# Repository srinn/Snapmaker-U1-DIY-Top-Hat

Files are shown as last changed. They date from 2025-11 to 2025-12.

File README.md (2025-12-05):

# Snapmaker U1 DIY Top Hat By. Srin
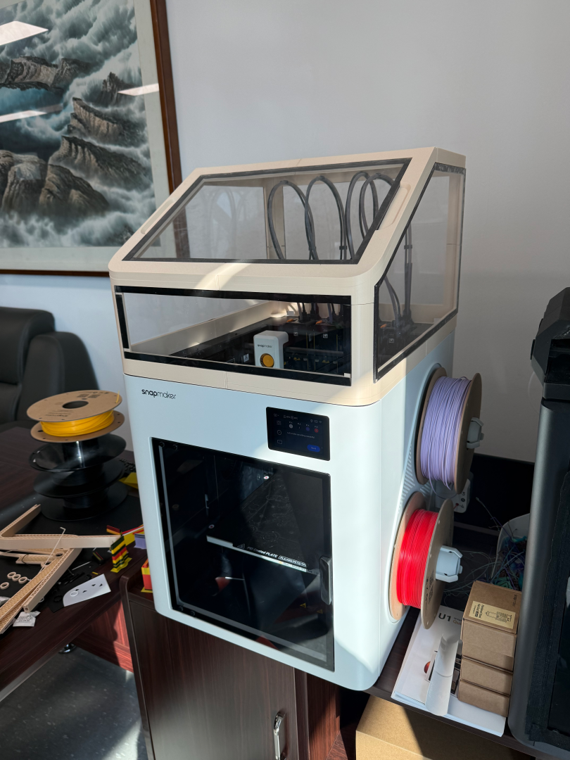
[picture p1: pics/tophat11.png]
tophat

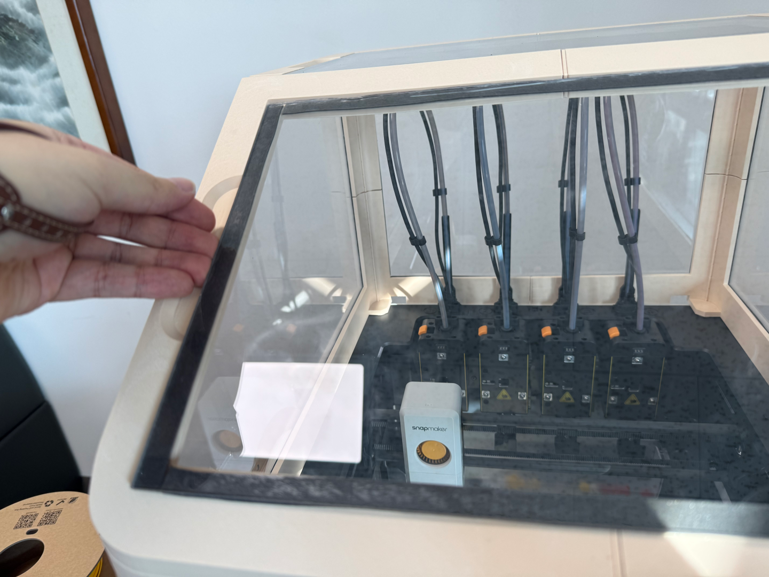
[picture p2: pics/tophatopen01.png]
tophat open

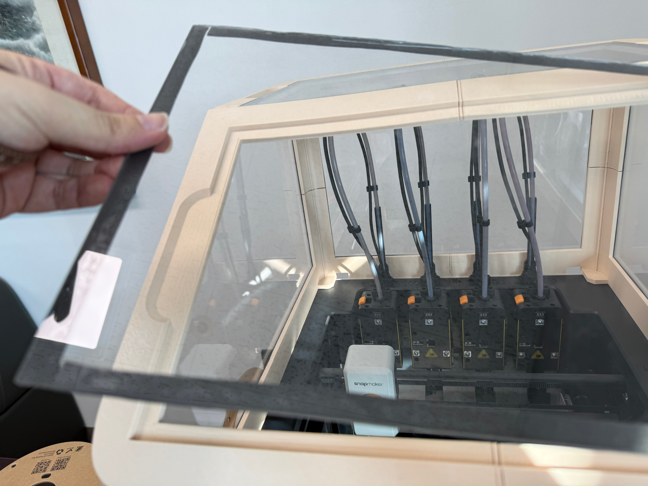
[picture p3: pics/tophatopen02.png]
tophat open

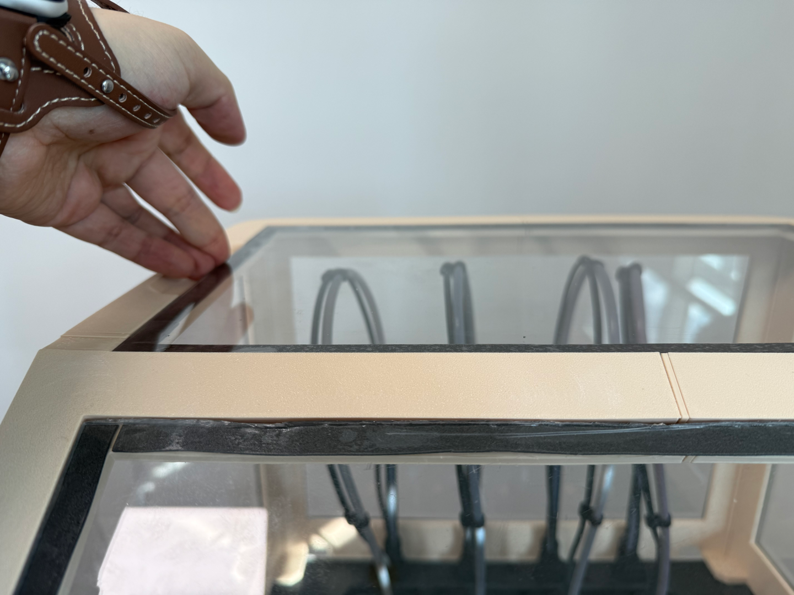
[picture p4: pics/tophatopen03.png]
tophat open

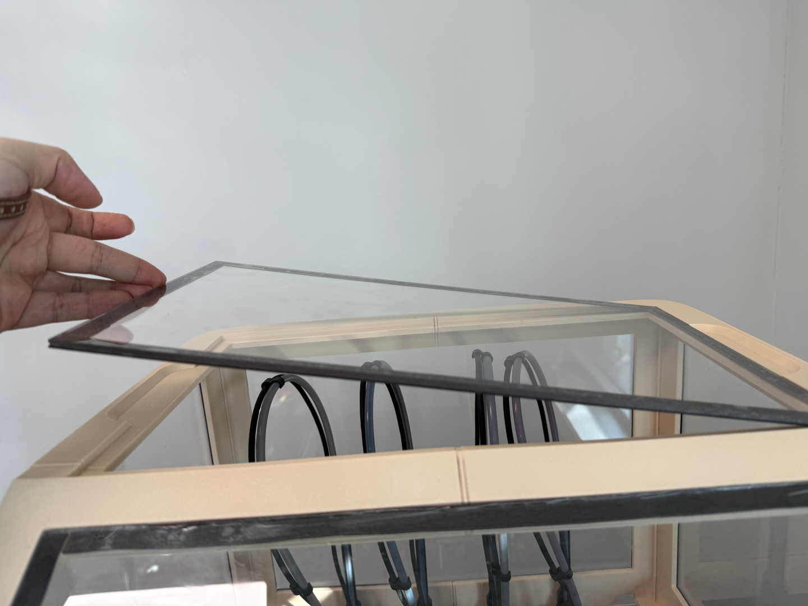
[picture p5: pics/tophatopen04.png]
tophat open

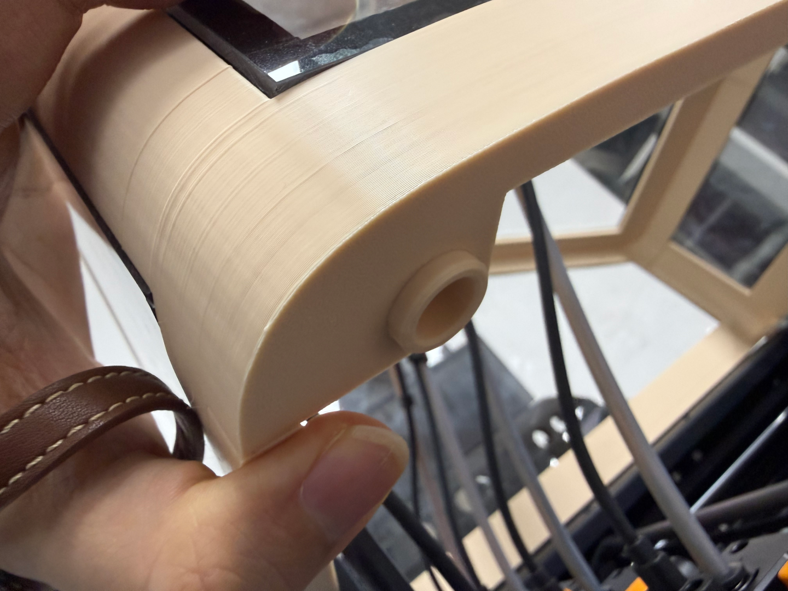
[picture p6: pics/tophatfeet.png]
tophat feet

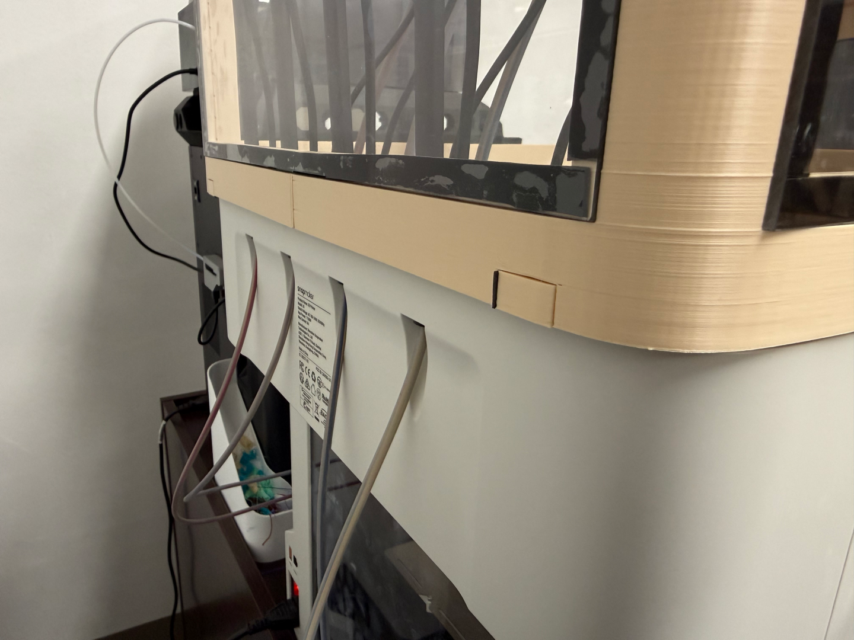
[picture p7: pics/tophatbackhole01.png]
tophat back hole

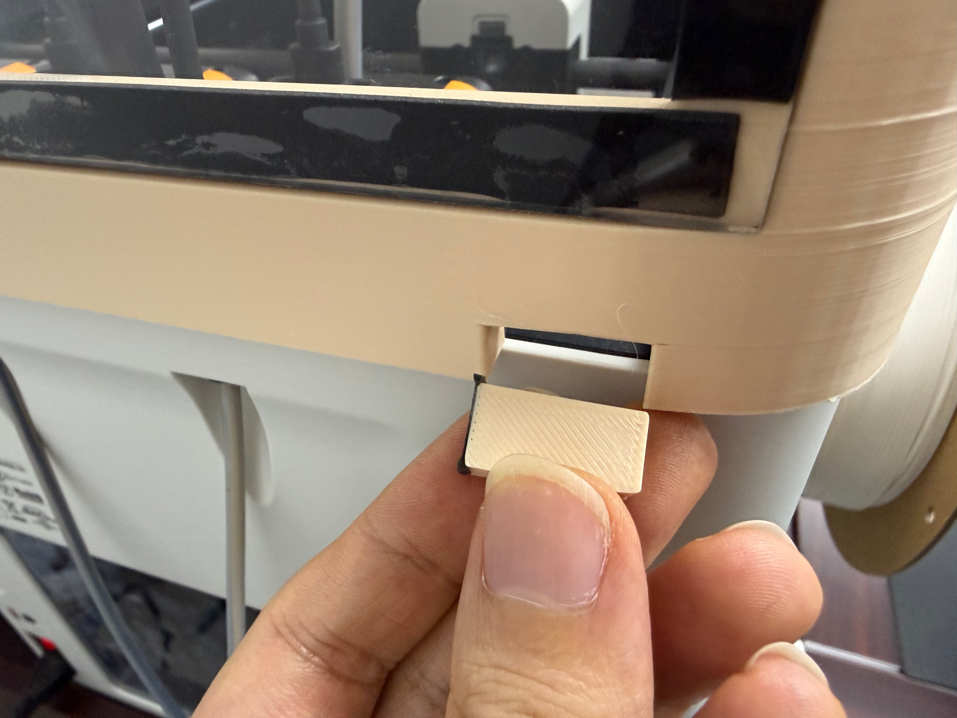
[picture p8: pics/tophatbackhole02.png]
tophat back hole

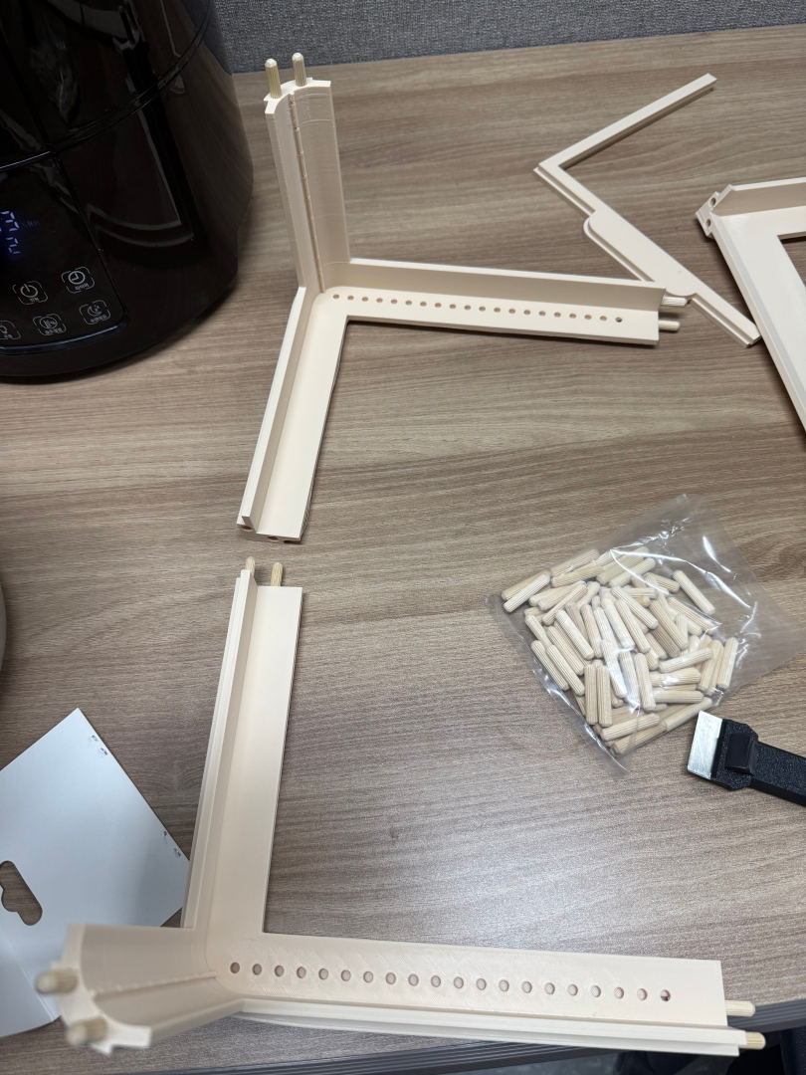
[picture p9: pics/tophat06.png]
tophat insert nut holes

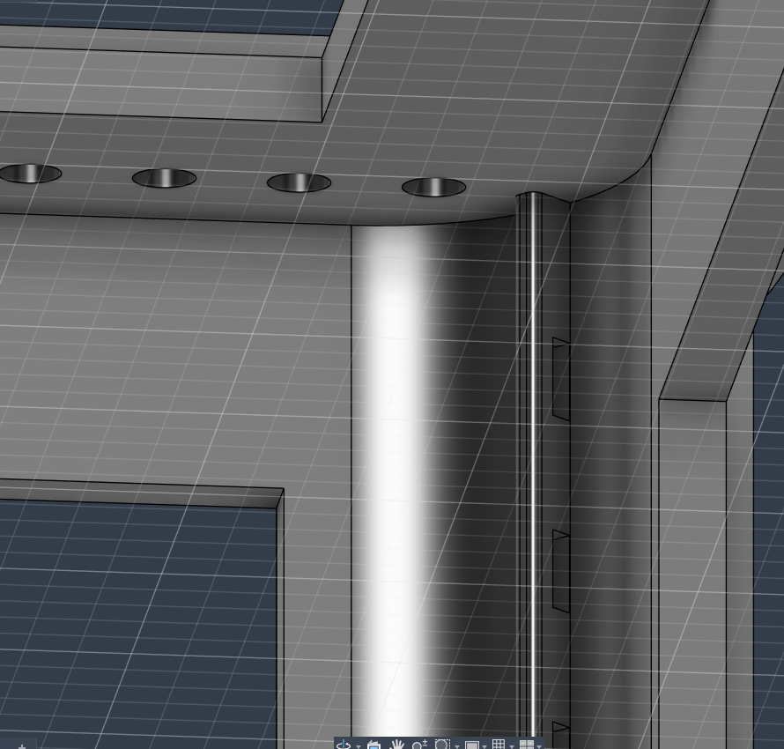
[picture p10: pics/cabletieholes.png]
tophat cable tie holes


Snapmaker U1 DIY Top Hat 입니다.</br>
This is a Snapmaker U1 DIY Top Hat.

[Printables](https://www.printables.com/model/1488431-snapmaker-u1-top-hat-by-srin)
[Makerworld](https://makerworld.com/ko/models/2022565-snapmaker-u1-top-hat-by-srin)

최소한 250mm 출력이 가능한 프린터가 필요합니다.</br>
A printer capable of printing at least 250mm is required.

- 저에게 커피 한 잔!</br>
Buy me a coffee!

"Buy Me A Coffee" (https://www.buymeacoffee.com/srin)

## BOM 구매처 / Ordering BOM
Blurolls와 협업하여 출력물을 제외한 BOM 키트를 구매할 수 있는 상품 페이지를 마련했습니다.</br>
In collaboration with Blurolls, we've created a product page where you can purchase the BOM kit, excluding the printed parts.

오리지널 모델, 비탈면이 긴 버전, 비탈면이 없는 버전의 총 세 종류의 모델을 지원합니다.</br>
Supports three types of models: Original Model, Huge Slope Version, and No Slope Version.

이 곳에서 BOM 키트를 주문하시면 저에게 직접적인 도움이 됩니다!</br>
Ordering a BOM kit here will directly help me!

물론 여전히 당신이 원하는 곳에서 자유롭게 PC 패널, 목공용 도웰핀, 3M VHB 테이프, 폼 테이프를 직접 주문할 수 있습니다!</br>
Of course, you can still freely order PC panels, wood dowel pins, 3M VHB tape, and foam tape directly from wherever you want!

아래의 Blurolls 링크를 클릭하여 주문하실 수 있습니다.</br>
You can order by clicking the Blurolls link below.

"Blurolls" (https://www.blurolls3d.com/products/snapmaker-u1-top-hat-pc-panels-kit-designed-by-srin)

## 중요 변경 사항 / Important change
1. 2025/11/24 PM 12:15 (GMT+0900, South Korea)
   - 중요한 변경 사항입니다.
STL 파일을 생성하고 업로드하기 전 어떤 이유에서인지 서포트 구조물이 정렬되지 않았습니다. 진심으로 사과드립니다.
서포트 구조물을 수정하여 다시 제작했습니다. 영향을 받은 출력물은 Upper Face STL 파일 4개입니다.
다시 한번 진심으로 사과드립니다.</br>
    This is an important change.
For some reason, the support structures were misaligned before the STL file was created and uploaded. I sincerely apologize.
I have corrected the support structures and recreated them. The affected prints are the four Upper Face STL parts.
Again, I sincerely apologize.
2. 2025/11/24 PM 02:37 (GMT+0900, South Korea)
   - 작은 프린터를 위한 모델이 추가되었습니다. 최소 180mm 이상의 프린터에서 출력 가능합니다. 목공용 도웰핀 직경 Ø6mm x 길이 30mm–40mm 를 48개 이상 준비하세요.</br>
     A model for small printers has been added. It can be printed on printers at least 180mm wide. Prepare at least 48 wooden dowel pins Ø6mm × length 30–40mm.</br>
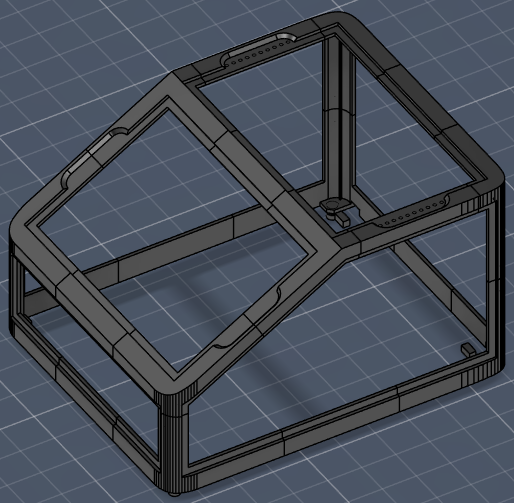
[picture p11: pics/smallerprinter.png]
smallerprinter
     
3. 2025/11/24 PM 05:30 (GMT+0900, South Korea)
   - Plexi glass 가 없는 모델이 추가되었습니다. 목공용 도웰핀 직경 Ø6mm x 길이 30mm–40mm 를 59개 이상 준비하세요.</br>
     Added models without Plexi glass. Prepare at least 59 wooden dowel pins Ø6mm × length 30–40mm.</br>
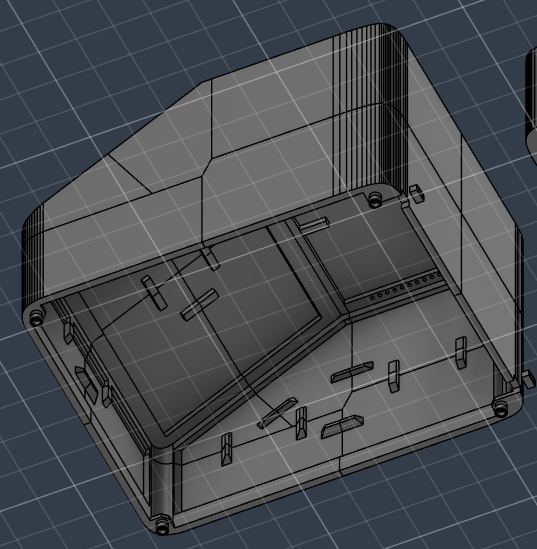
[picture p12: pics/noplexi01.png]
noplexi
     </br>
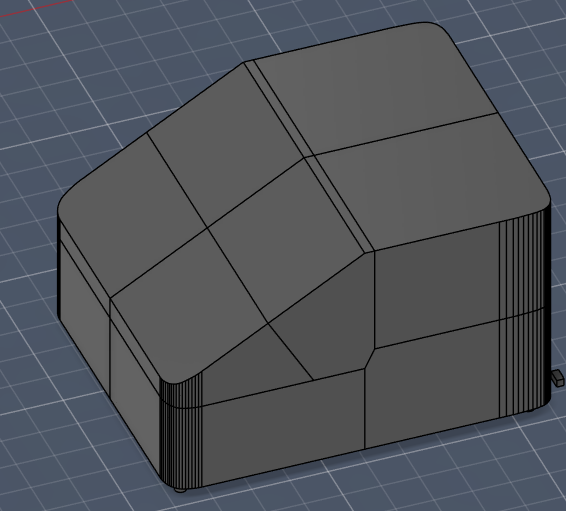
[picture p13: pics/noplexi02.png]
noplexi
     
4. 2025/11/24 PM 06:39 (GMT+0900, South Korea)
   - 비탈면이 없이 꼭대기가 평평한 모델이 추가되었습니다. 목공용 도웰핀 직경 Ø6mm x 길이 30mm–40mm 를 24개 이상 준비하세요.</br>
     Added a model with a flat top and no slope. Prepare at least 24 wooden dowel pins Ø6mm × length 30–40mm.</br>
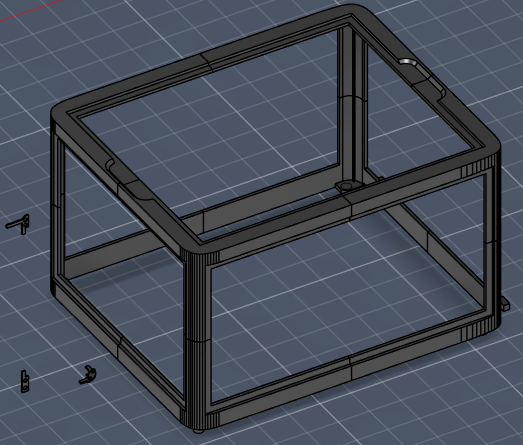
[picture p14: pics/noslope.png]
noslope
     </br>
     비탈면 없는 버전 모델 전용 PC 패널 사이즈는 다음과 같습니다.</br>
     PC panel sizes for No slope version model only are as follows:
       - 상단 덮개 PC 패널 3T 363mm × 457mm – 1개</br>
         Top cover PC panel 3T 363mm × 457mm – 1 pcs
       - 앞면 및 뒷면 PC 패널 3T 363mm × 254mm – 2개</br>
         Front and Rear PC panel 3T 363mm × 254mm – 2 pcs
       - 사이드 PC 패널 3T 461mm × 254mm – 2개</br>
         Side PC panels 3T 461mm × 254mm – 2 pcs
5. 2025/11/28 PM 11:48 (GMT+0900, South Korea)
   - 정면 Plexi glass 가 없고 비탈면이 긴 모델이 추가되었습니다. 목공용 도웰핀 직경 Ø6mm x 길이 30mm–40mm 를 24개 이상 준비하세요.</br>
     A model without front Plexi glass and with a long slope has been added. Prepare at least 24 wooden dowel pins Ø6mm × length 30–40mm.</br>
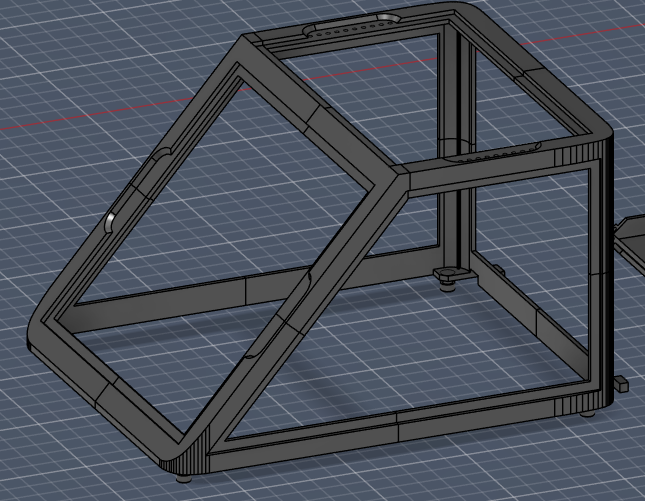
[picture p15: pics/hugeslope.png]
hugeslope
     </br>
     비탈면이 긴 버전 모델 전용 PC 패널 사이즈는 다음과 같습니다.</br>
     PC panel sizes for Huge slope version model only are as follows:
       - 상단 덮개 PC 패널 3T 363mm × 228mm – 1개</br>
         Top cover PC panel 3T 363mm × 228mm – 1 pcs
       - 상단 비탈면 덮개 PC 패널 3T 363mm × 336mm – 1개</br>
         Top sloped cover PC panel 3T 363mm × 336mm – 1 pcs
       - 뒷면 PC 패널 3T 363mm × 259mm – 1개</br>
         Front and Rear PC panel 3T 363mm × 259mm – 1 pcs
       - 사이드 PC 패널 3T 445mm × 259mm – 2개 (대각선 절단 219mm) **주의사항: 도면을 참고하세요.**</br>
         Side PC panels 3T 445mm × 259mm – 2 pcs (diagonal cut 219mm) **Important: refer to the drawings.**</br>
         사이드 PC 패널</br>
         Side PC Panel</br>
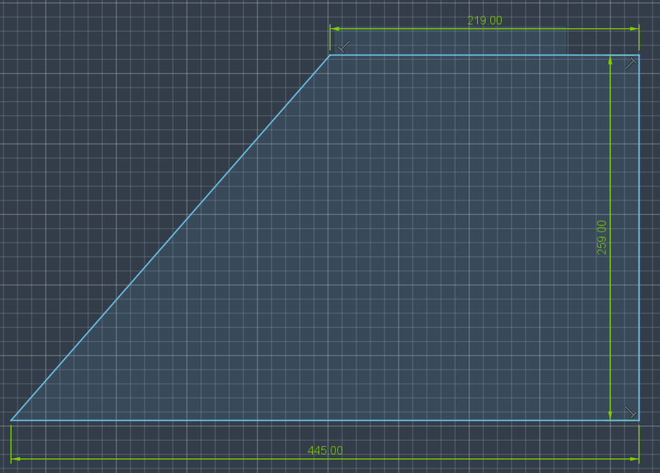
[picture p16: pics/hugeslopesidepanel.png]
sidepanel
         
6. 2025/12/05 PM 01:17 (GMT+0900, South Korea)
   - 정면, 비탈면 Plexi glass 만 존재하는 모델이 추가되었습니다. 목공용 도웰핀 직경 Ø6mm x 길이 30mm–40mm 를 52개 이상 준비하세요.</br>
     A model with only Plexi glass on the front and slope sides has been added. Prepare at least 52 wooden dowel pins Ø6mm × length 30–40mm.</br>
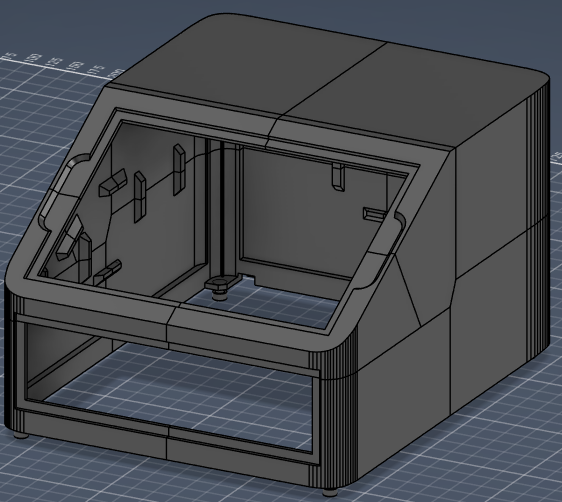
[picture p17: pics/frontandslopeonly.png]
frontandslopeonly
     </br>
     Front and slope plexiglass only version 모델은 오리지널 모델과 사이즈를 공유합니다. PC 패널 사이즈는 다음과 같습니다.</br>
     The Front and Slope Plexiglass Only version shares the same dimensions as the original model. The PC panel sizes are as follows:
       - 상단 비탈면 덮개 PC 패널 3T 363mm × 242mm – 1개</br>
         Top sloped cover PC panel 3T 363mm × 242mm – 1 pcs
       - 앞면 PC 패널 3T 363mm × 108mm – 1개</br>
         Front PC panel 3T 363mm × 108mm – 1 pcs
7. 2025/12/05 PM 04:20 (GMT+0900, South Korea)
   - 비탈면이 긴 모델의 변형이 추가되었습니다. 비탈면을 제외한 곳에 6T PC 패널을 사용합니다. 목공용 도웰핀 직경 Ø6mm x 길이 30mm–40mm 를 24개 이상 준비하세요.</br>
     A variant of the Huge Slope model has been added. It uses 6T PC panels on all surfaces except the slope. Prepare at least 24 wooden dowel pins Ø6mm × length 30–40mm.</br>
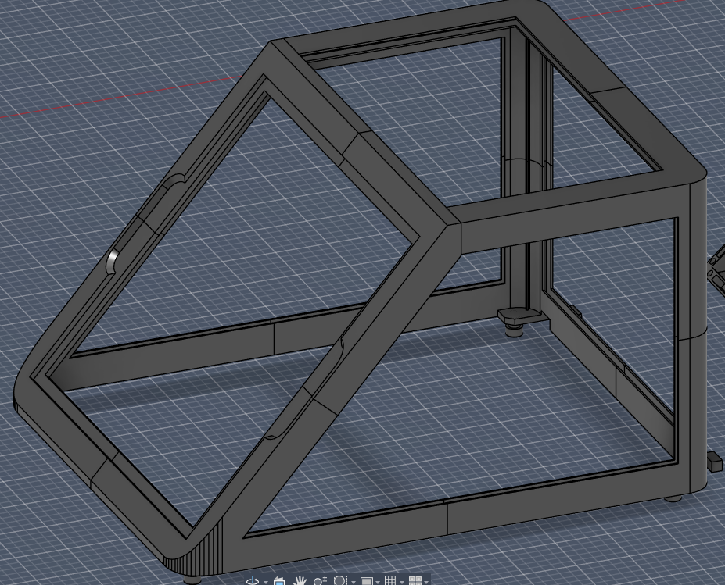
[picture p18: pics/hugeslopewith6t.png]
hugeslopewith6t
     </br>
     비탈면이 긴 6T Plexiglass 모델 전용 PC 패널 사이즈는 다음과 같습니다.</br>
     PC panel sizes for Huge slope with 6T plexiglass version model only are as follows:
       - 상단 덮개 PC 패널 6T 363mm × 227mm – 1개</br>
         Top cover PC panel 6T 363mm × 227mm – 1 pcs
       - 상단 비탈면 덮개 PC 패널 3T 363mm × 336mm – 1개</br>
         Top sloped cover PC panel 3T 363mm × 336mm – 1 pcs
       - 뒷면 PC 패널 6T 363mm × 259mm – 1개</br>
         Front and Rear PC panel 6T 363mm × 259mm – 1 pcs
       - 사이드 PC 패널 6T 445mm × 259mm – 2개 (대각선 절단 219mm) **주의사항: 도면을 참고하세요.**</br>
         Side PC panels 6T 445mm × 259mm – 2 pcs (diagonal cut 219mm) **Important: refer to the drawings.**</br>
         사이드 PC 패널</br>
         Side PC Panel</br>
         sidepanel

## 기능 / Features
- 출력물 상단에 10mm 간격으로 3x4x5 인서트 너트 구멍을 뚫어두었습니다.</br>
챔버 히터 등 각자 필요한 구조물을 설계하여 Top Hat의 상단에 추가할 수 있습니다.</br>
케이블 타이로 케이블을 정리할 수 있습니다.</br>
There are insert nut holes (3x4x5) spaced 10mm apart on the top of the printed parts.</br>
You can design additional structures such as a chamber heater and attach them onto the top of the Top Hat.</br>
You can organize cables using cable ties.

- 출력물 하단에 케이블 통과용 구멍을 뚫어두었습니다.</br>
필요한 구조물을 설계한 후 이 구멍을 통해 케이블을 지나가게 할 수 있습니다.</br>
A cable pass-through hole is provided at the bottom of the printed parts.</br>
You can route cables through this hole after designing any required components.

- 상단과 상단 비탈면의 덮개에 손가락 구멍을 뚫어두었습니다.</br>
이곳에 폼 테이프를 붙인 패널을 올려 사용하고, 필요하면 언제든지 패널을 쉽게 제거할 수 있습니다.</br>
Finger holes are included on the top covers and sloped top covers.</br>
You can place panels with foam tape on these holes and easily remove them whenever needed.

- 출력물 하단에 끼우는 4개의 고정용 발 구조물을 통해 U1의 상단에 위치한 고무 패킹에 고정할 수 있습니다.</br>
The four mounting feet inserted at the bottom of the printed parts allow the Top Hat to be secured to the rubber packing located on top of the U1.

## BOM
- 목공용 도웰핀 직경 Ø6mm x 길이 30mm–40mm 30개 (30개보다 여유있게 준비하세요)</br>
30 wooden dowel pins Ø6mm × length 30–40mm (prepare more than 30 just in case)
- 3M VHB 양면테이프 폭 10mm</br>
3M VHB double-sided tape, width 10mm
- 폼 테이프 두께 1mm 폭 10mm (글쓴이는 20mm 짜리를 사서 세로로 잘라 10mm로 사용했습니다)</br>
Foam tape thickness 1mm, width 10mm (I bought 20mm and cut it vertically to 10mm)
- 상단 비탈면 덮개 PC 패널 3T 363mm × 242mm – 1개</br>
Top sloped cover PC panel 3T 363mm × 242mm – 1 pcs
- 상단 덮개 PC 패널 3T 363mm × 228mm – 1개</br>
Top cover PC panel 3T 363mm × 228mm – 1 pcs
- 뒷면 PC 패널 3T 363mm × 254mm – 1개</br>
Rear PC panel 3T 363mm × 254mm – 1 pcs
- 앞면 PC 패널 3T 363mm × 108mm – 1개</br>
Front PC panel 3T 363mm × 108mm – 1 pcs
- 사이드 PC 패널 3T 461mm × 254mm – 2개 (대각선 절단 223mm, 116mm) **주의사항: 도면을 참고하세요.**</br>
Side PC panels 3T 461mm × 254mm – 2 pcs (diagonal cut 223mm, 116mm) **Important: refer to the drawings.**

사이드 PC 패널</br>
Side PC Panel

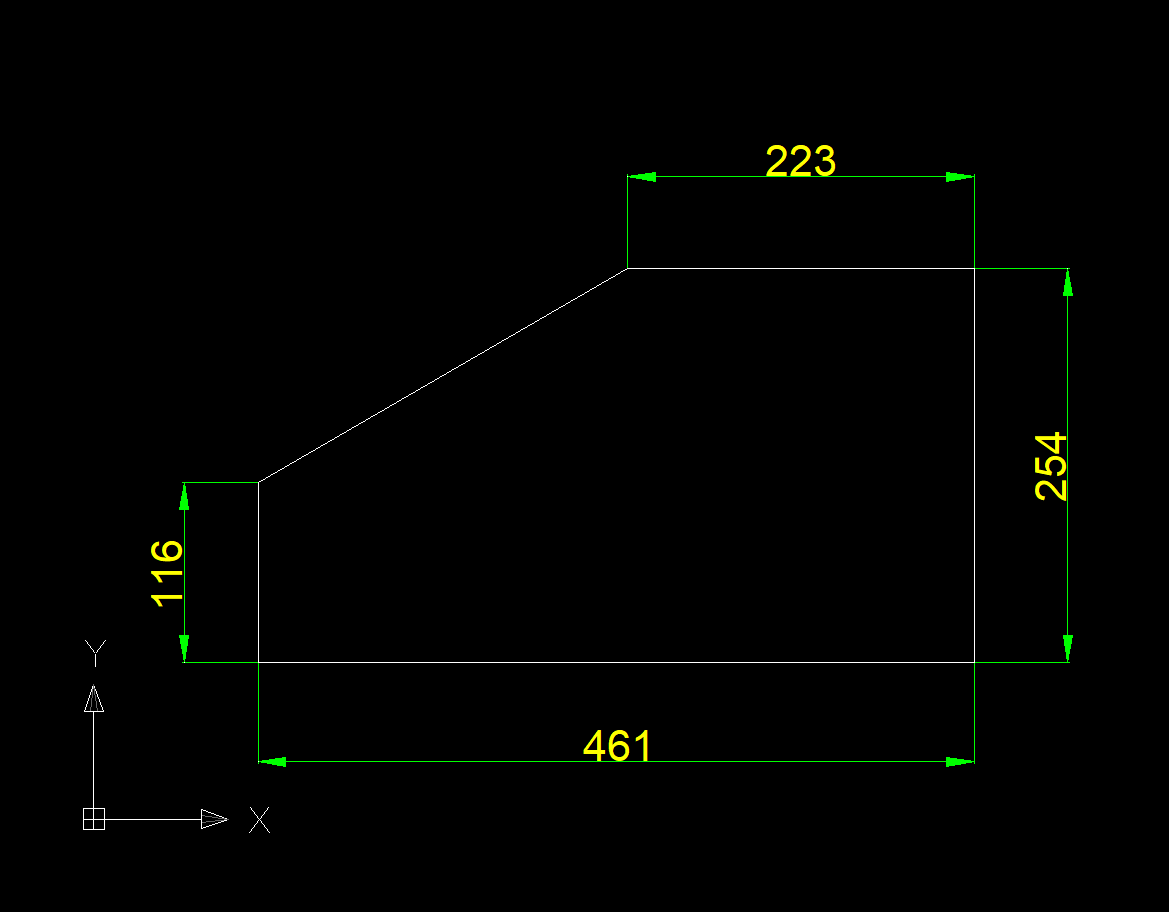
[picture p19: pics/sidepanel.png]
sidepanel


위의 BOM에 적혀 있는 사이드 패널의 크기는 각 구멍의 크기보다 1mm 작습니다.</br>
The side panel dimensions in the BOM are 1mm smaller than the hole sizes.

예를 들어, 원래 설계된 상단 비탈면 덮개 출력물의 구멍 크기는 364mm × 243mm 입니다.</br>
For example, the opening for the original top sloped cover is 364mm × 243mm.

패널을 주문하실 때 참고하세요.</br>
Please keep this in mind when ordering panels.

## 출력 / Printing
PLA는 내열 온도가 55도 부근이므로 가급적 사용하지 않는 것을 추천합니다. 저는 ABS로 출력했습니다.</br>
PLA has a heat resistance around 55°C, so it is not recommended. I printed using ABS.

- 벽 수: 4레이어</br>
Wall count: 4 layers
- 상단 레이어: 5겹</br>
Top layers: 5
- 하단 레이어: 5겹</br>
Bottom layers: 5
- 내부 채움: 15%</br>
Infill: 15%

Upper Face, Upper Top 출력물의 경우 오버행을 위한 서포트가 미리 배치되어 있습니다.</br>
The Upper Face and Upper Top models include pre-placed supports for overhangs.

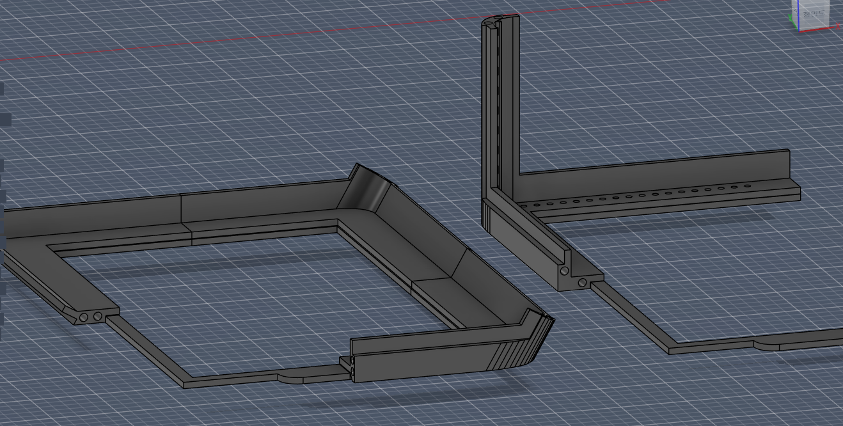
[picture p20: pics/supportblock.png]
support block


출력물을 조립했을 때 전체 크기는 가로 413mm, 세로 507mm 이어야 합니다.</br>
Assembled dimensions should be 413mm (width) × 507mm (length).

프린터에 따라 출력 후 조립했을 때 전체 길이가 설계도에 의도된 길이보다 모자랄 수 있습니다.</br>
Depending on your printer, the total length may end up shorter than designed.

길이가 짧은 부위의 Spacer 출력물을 본인이 필요한 길이에 맞게 슬라이서에서 z 높이를 조정하여 출력한 후</br>
For short areas, adjust the Z height of the spacer model in the slicer

도웰핀으로 연결된 연결부위 사이에 끼워서 길이를 늘여 사용하세요.</br>
Print and insert it between connected parts with dowel pins to extend length.

Spacer 출력 방법은 Spacer 출력 방법 섹션을 참고하세요.</br>
Refer to the Spacer printing section below.

일부 모델은 구조상 Spacer 를 만들 수 없습니다. 따라서 Spacer 가 존재하지 않을 수도 있습니다.</br>
Some models are structurally unable to create a Spacer, so a Spacer may not exist.

출력물의 전체 크기가 설계된 길이보다 크면 U1 상단의 고무 패킹에 커버의 발을 끼울 수 없을 수도 있습니다.</br>
If the total size is longer than intended, the feet may not fit into the rubber packing on the U1 top.

출력물이 실제보다 크게 나오지 않게 주의해 주세요.</br>
Ensure prints do not come out oversized.

길고 얇은 막대 모양의 네모 모양 출력물을 최대한 길게 출력해서 그 출력물의 길이가 의도한 길이가 맞는지 재 보세요.</br>
Print a long rectangular bar and measure to confirm accuracy.

만약 출력물의 길이가 의도한 길이보다 길게 나온다면 Top Hat 출력 시 전체 크기를 약간 줄여 출력하세요.</br>
If it prints longer, reduce the overall scale slightly when printing the Top Hat.

예를 들어 X축으로 200mm인 긴 출력물을 출력하고 그 출력물을 측정했을 때의 길이가 201mm라면,</br>
Example: If a 200mm bar prints as 201mm,

200 ÷ 201 = 0.99502 = 99.502% 이므로 Top Hat 출력물의 전체 크기를 99.5% 이하로 변경해 출력하세요.</br>
200 ÷ 201 = 0.99502 = 99.502% → scale to ~99.5% or slightly less for Top Hat.

(2025/12/05) 전체 길이를 측정하고 출력물의 축척을 계산하기 위한 모델을 추가하였습니다.</br>
(2025/12/05) Added a model to measure the overall length and calculate the scale of the output.
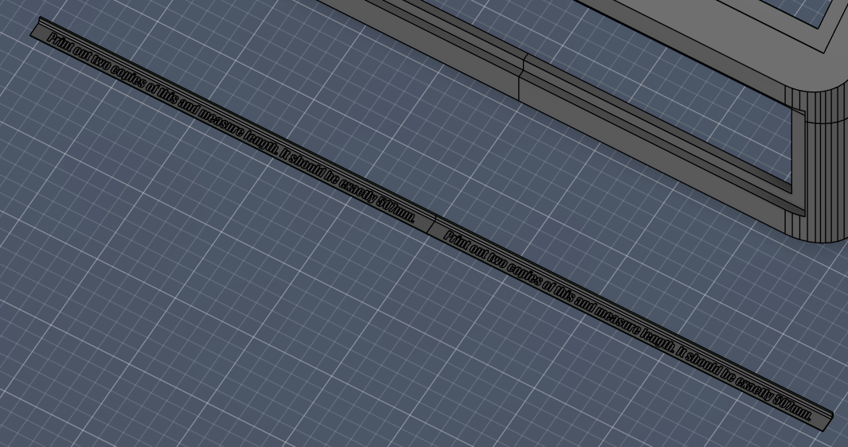
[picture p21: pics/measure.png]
measure


ETC/Calibrate.stl 파일을 내려받아 2개 출력한 후 전체 길이를 측정하세요.</br>
Download the ETC/Calibrate.stl file, print two copies, and measure the total length.

측정된 전체 길이가 502.4mm 였다면 507 ÷ 502.4 = 1.00915 = 100.91% 를 계산한 후 이 스케일을 모든 출력물에 적용하세요.</br>
If the measured total length was 502.4mm, calculate 507 ÷ 502.4 = 1.00915 = 100.91% and apply this scale to all outputs.

확실히 맞는 값인지 확인하고 싶다면 Calibrate.stl 의 스케일을 변경하여 다시 한 번 출력해 보세요.</br> 
If you want to make sure that the values are correct, try changing the scale of Calibrate.stl and printing it again.

너무 작게 출력하지 마세요! 조립할 수 없을 수도 있습니다.</br>
Do not scale too small! It may prevent assembly.

feet.stl 파일은 Top Hat을 U1 상단의 고무 패킹에 고정하기 위한 출력물입니다. 4개 출력하세요.</br>
feet.stl is used to secure the Top Hat to the rubber packing on the U1 top. Print 4 pieces.

tophat feet

## 조립 / Assembly

**Top Hat 출력물에 3M VHB 양면 테이프를 붙이기 전에 반드시 출력물의 길이가 맞는지 확인하세요!**</br>
**Before applying 3M VHB tape, make sure the printed length is correct!**

1. 모든 출력물을 출력 후 구멍을 따라 도웰핀을 끼워 조립하세요.</br>
After printing all parts, insert dowel pins through the holes to assemble.

2. 4개의 feet.stl 출력물을 Top Hat 바닥면의 4개의 구멍에 끼우세요.</br>
Insert the 4 feet.stl pieces into the four holes at the bottom.

3. 여기까지 조립된 Top Hat을 U1에 올려 고무 패킹 위치에 Top Hat의 발을 끼우세요. 이 때 잘 맞지 않는다면 중간 연결 부위를 살짝 빼세요.</br>
Place the partially assembled Top Hat on the U1 and insert the feet into the rubber packing. If it doesn’t fit well, slightly disconnect joints.

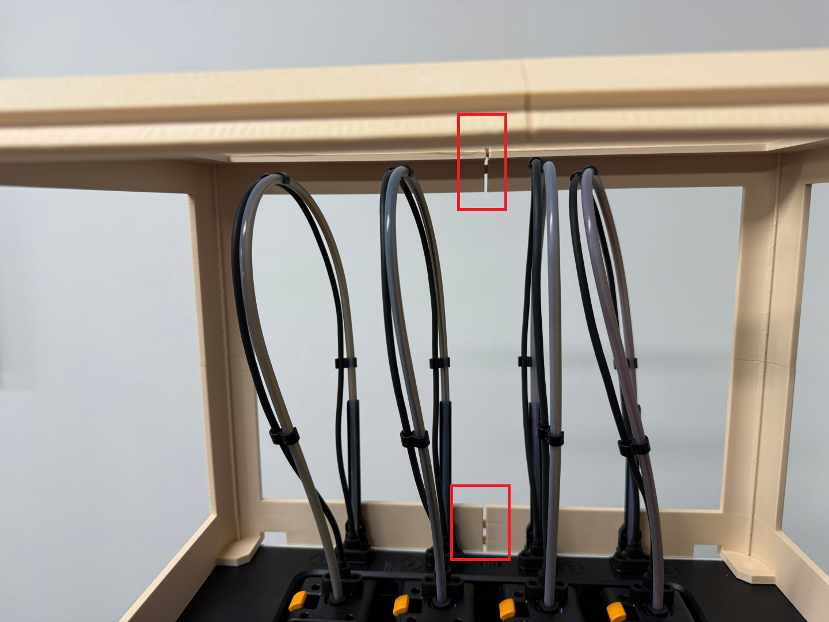
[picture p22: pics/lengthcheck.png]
length check


4. 출력물의 중간 연결 부위가 벌어지는 지점들이 있다면 벌어지는 지점의 길이를 재서 기록하세요.</br>
PC 패널들도 한번씩 끼워 보세요.</br>
If any joint gaps appear, measure and record the needed length.</br>
Also test-fit the PC panels.

5. 모든 지점들을 측정하고 기록했다면 맨 하단의 Spacer 출력 방법 섹션으로 가서 필요한 Spacer를 출력하세요.</br>
여기까지 Top Hat이 잘 준비되었다면 계속 진행하세요.</br>
After measuring all points, go to the Spacer printing section and print required spacers.</br>
If everything fits well so far, continue.

6. 상단 비탈면 덮개 PC 패널, 상단 덮개 PC 패널의 테두리에는 폼 테이프를 붙이세요.</br>
손으로 들어서 패널을 제거할 수 있도록 양면 테이프를 붙이지 않고 폼 테이프를 붙여야 합니다. </br>
Attach foam tape along the edges of the top sloped and top cover PC panels.</br>
Do NOT use double-sided tape here — use foam tape so the panels can be removed by hand.

7. 그 외의 PC 패널의 테두리에는 3M VHB 양면 테이프를 붙이고 Top Hat의 각 구멍에 맞게 잘 붙이세요.</br>
Apply 3M VHB tape to all other PC panel edges and attach them securely to the corresponding openings.

## Spacer 출력 방법 / How to Print Spacers

슬라이서 프로그램에서 spacer.stl 파일을 불러오세요. Spacer 파일에는 각 조각들이 필요한 원래의 위치에 배치되어 있습니다.</br>
Load spacer.stl into your slicer. The pieces are arranged in their original intended positions.

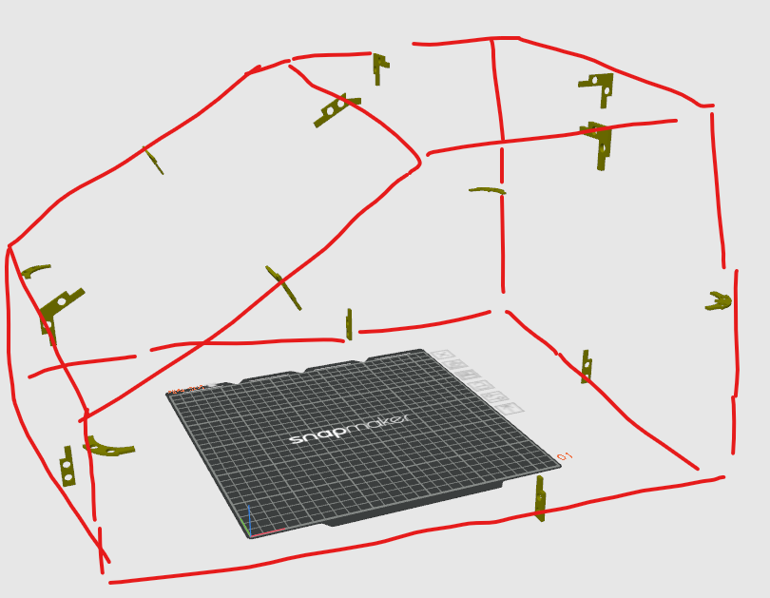
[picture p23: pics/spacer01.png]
spacer


Spacer를 각각의 객체로 분할해 주세요.</br>
Separate each spacer into individual objects.

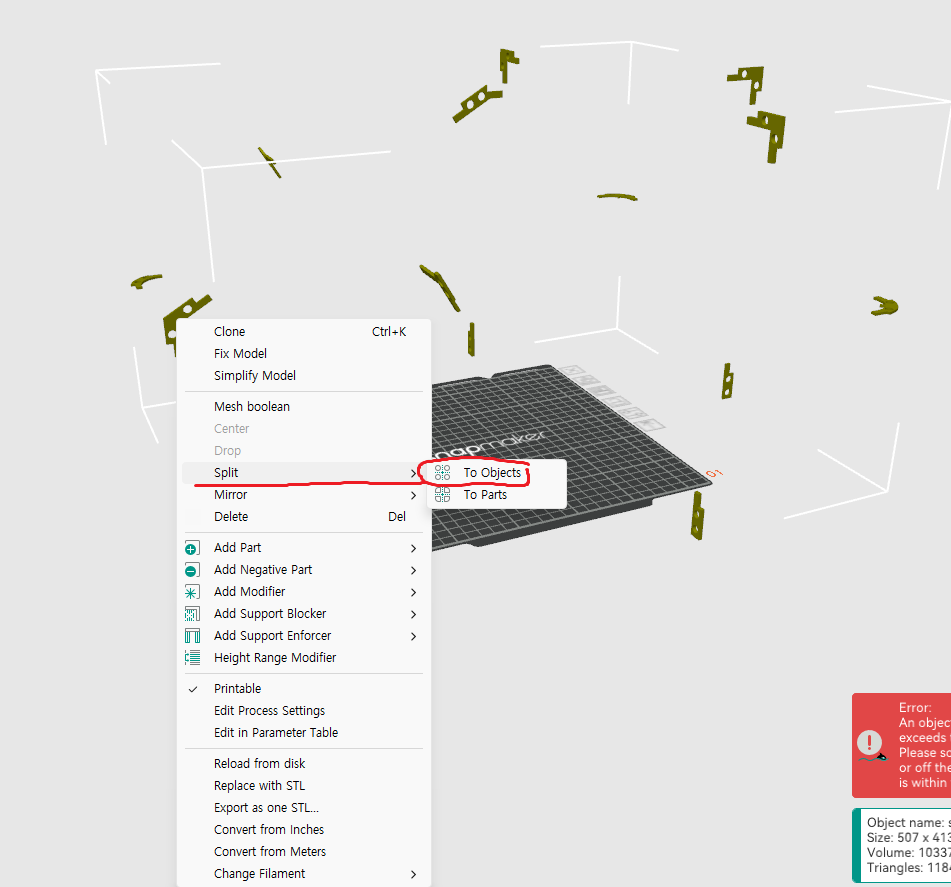
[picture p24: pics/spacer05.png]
spacer


이 중 필요한 Spacer 객체를 가져온 후 자동 방향 지정 기능으로 프린터 베드에 놓습니다.</br>
Select the needed spacer(s) and auto-orient them on the print bed.

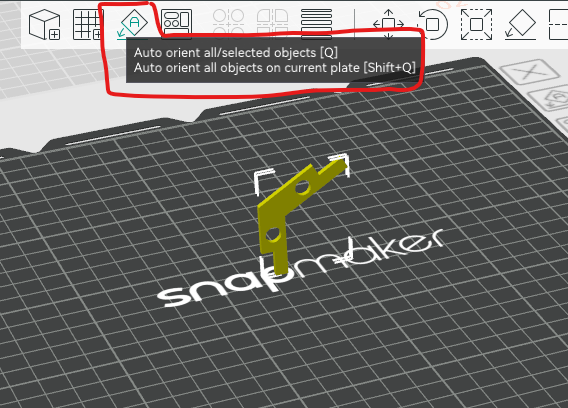
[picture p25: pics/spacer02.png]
spacer


Spacer 부품을 원하는 길이만큼 수정하기 위해 배율 기능을 사용합니다.</br>
Use the scale function to adjust the part length.

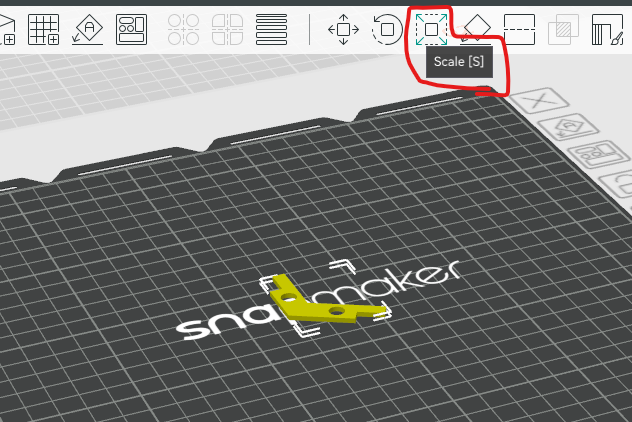
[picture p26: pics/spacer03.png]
spacer


필요한 길이만큼 Z높이값을 변경합니다.</br>
Modify the Z-height to the required length.

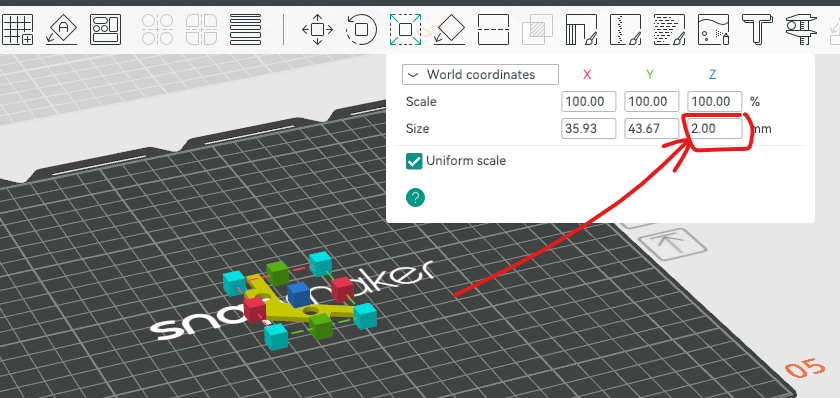
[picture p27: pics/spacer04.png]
spacer


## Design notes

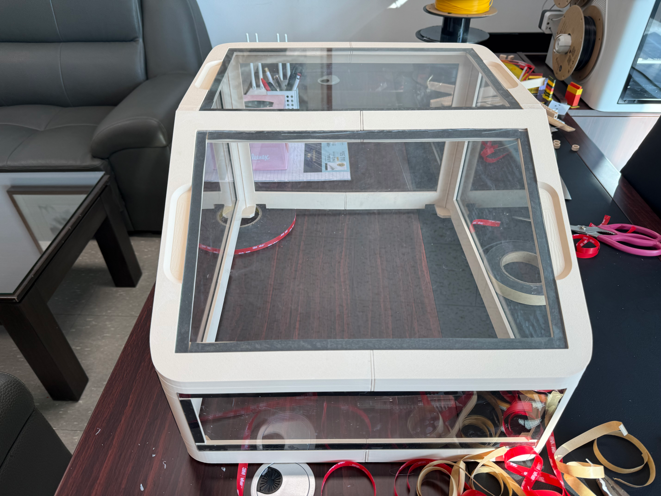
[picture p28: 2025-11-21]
pics/tophat10.png

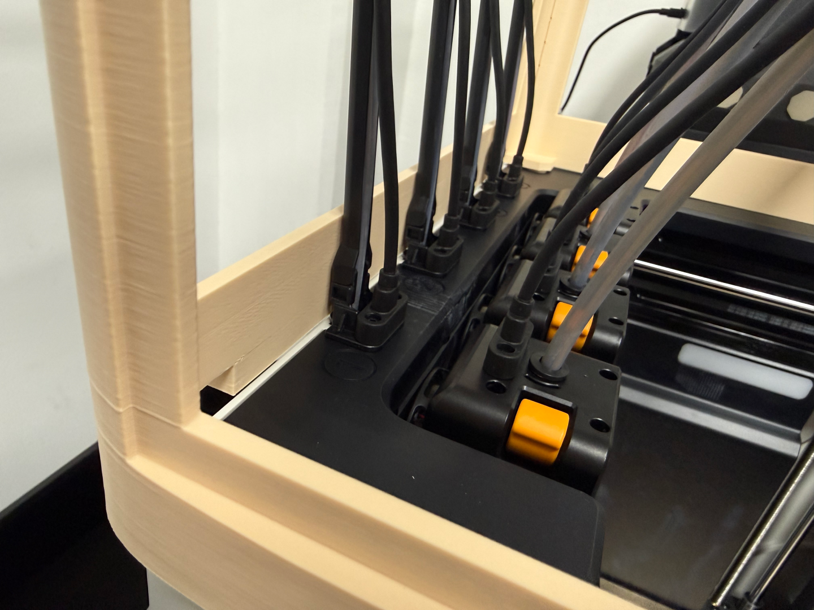
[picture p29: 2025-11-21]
pics/tophat04.png

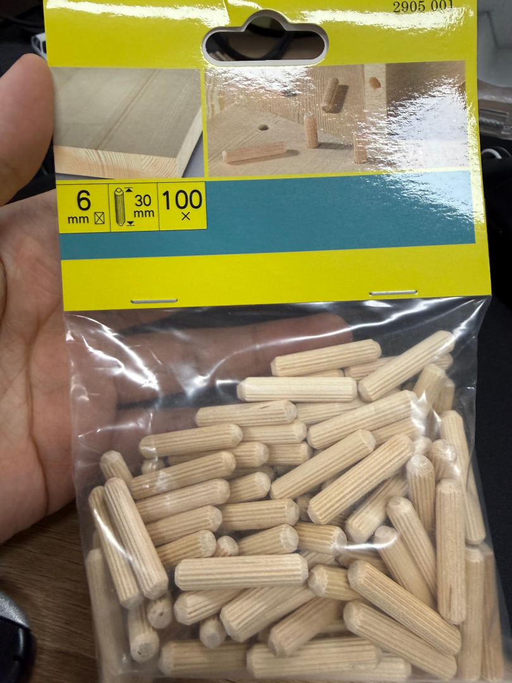
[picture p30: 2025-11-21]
pics/wooden_dowel_pin.png

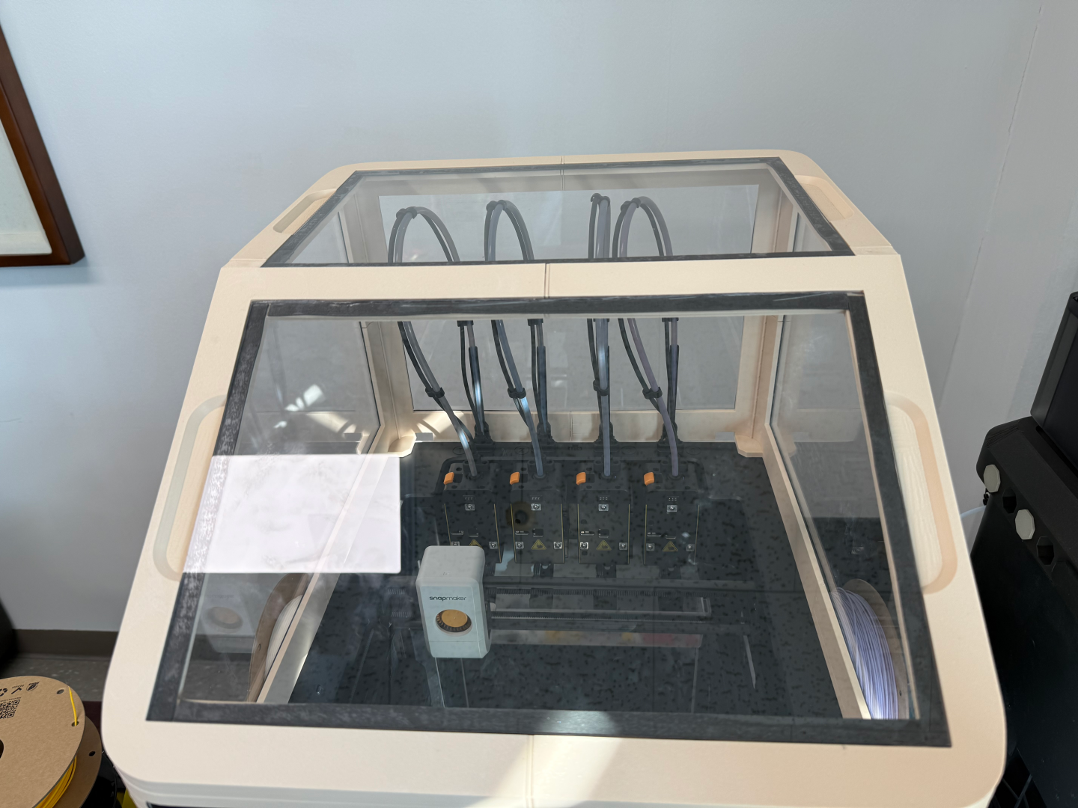
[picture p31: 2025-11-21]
pics/tophat12.png

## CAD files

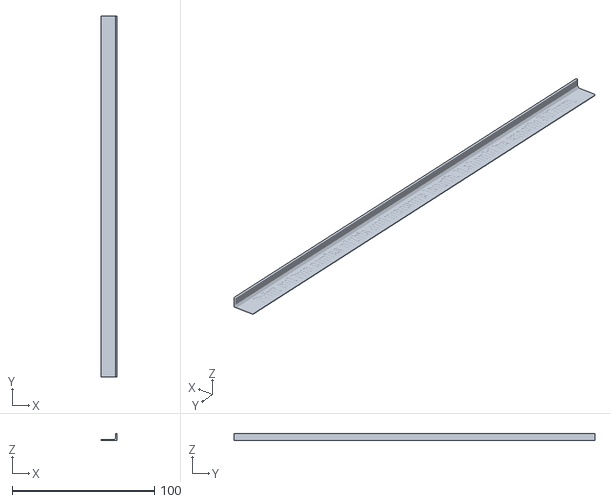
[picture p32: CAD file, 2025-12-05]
ETC/Calibrate.stl
11.0 x 253.5 x 5.00

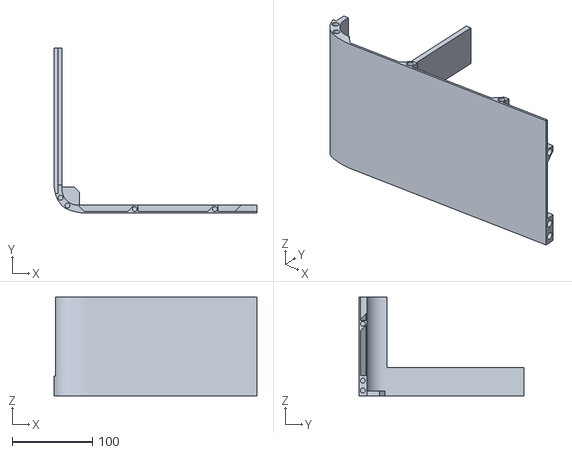
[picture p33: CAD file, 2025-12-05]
Front and slope plexiglass only version/Front Face (Right).stl
253.5 x 206.5 x 123.5

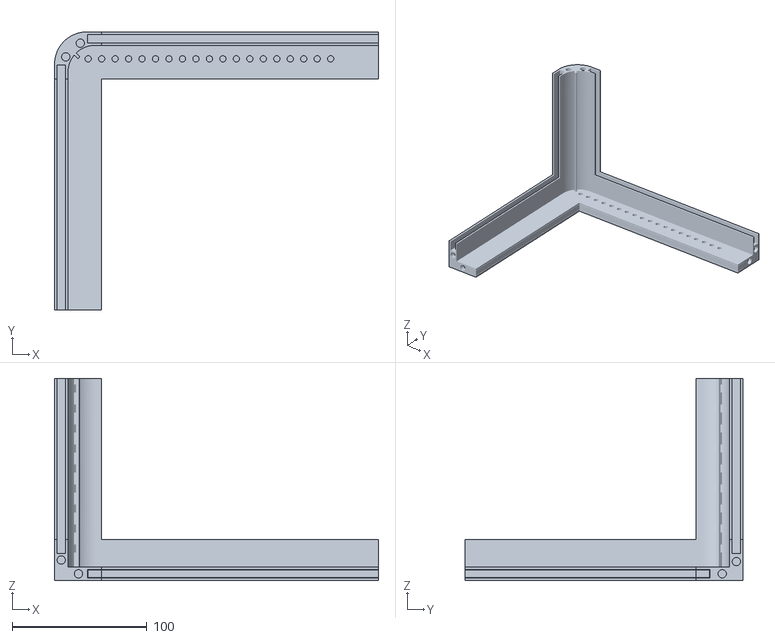
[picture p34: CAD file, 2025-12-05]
Huge slope 6mm plexiglass version/Top (Left).stl
240.5 x 206.5 x 150.0

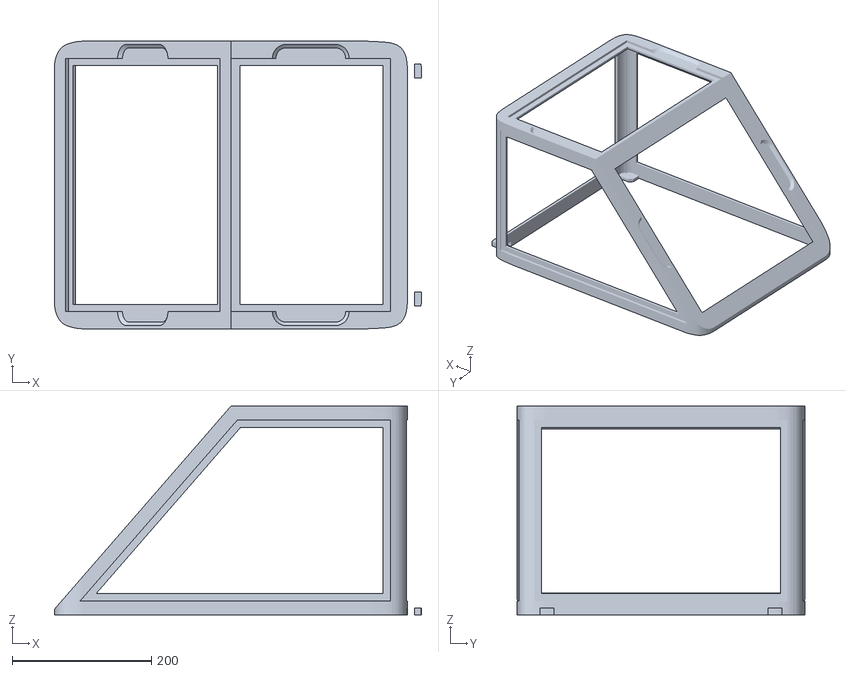
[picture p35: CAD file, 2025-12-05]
Huge slope one piece version/Huge slope one piece version.stl
527.0 x 413.1 x 300.0

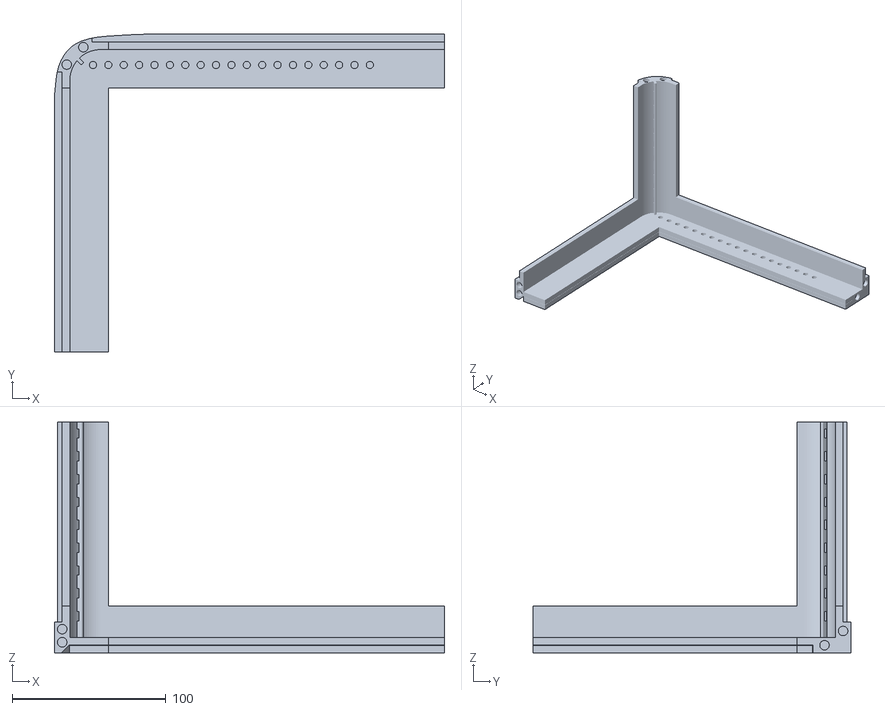
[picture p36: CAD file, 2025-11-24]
No slope version/Upper Back (Left).stl
253.5 x 206.6 x 150.0

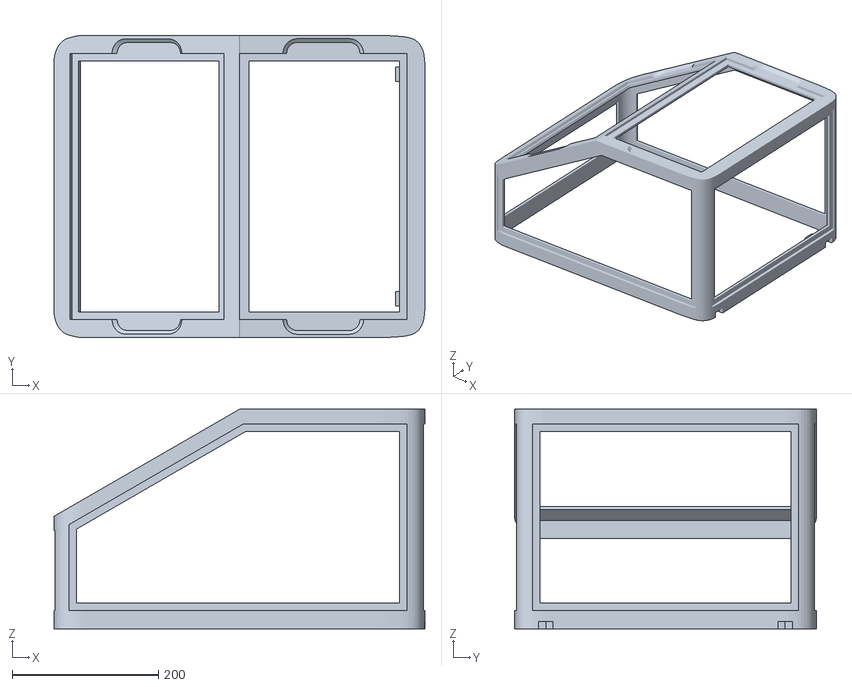
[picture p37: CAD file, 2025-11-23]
One piece version/One piece version.stl
507.0 x 413.1 x 300.0

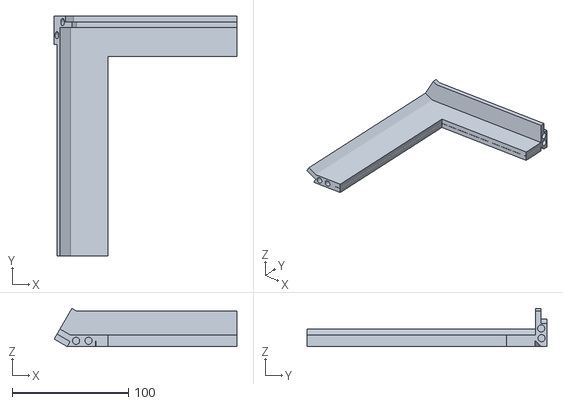
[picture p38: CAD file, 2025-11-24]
Original version/Upper Face (Left Up).stl
157.3 x 206.5 x 32.9

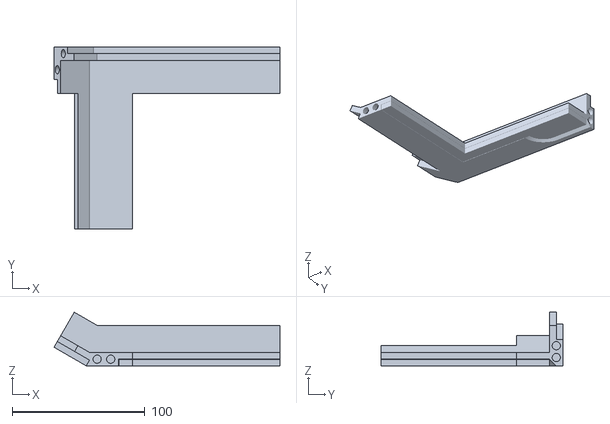
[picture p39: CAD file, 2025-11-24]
Smaller printer version/Upper Face (Left Up).stl
170.2 x 137.0 x 40.4

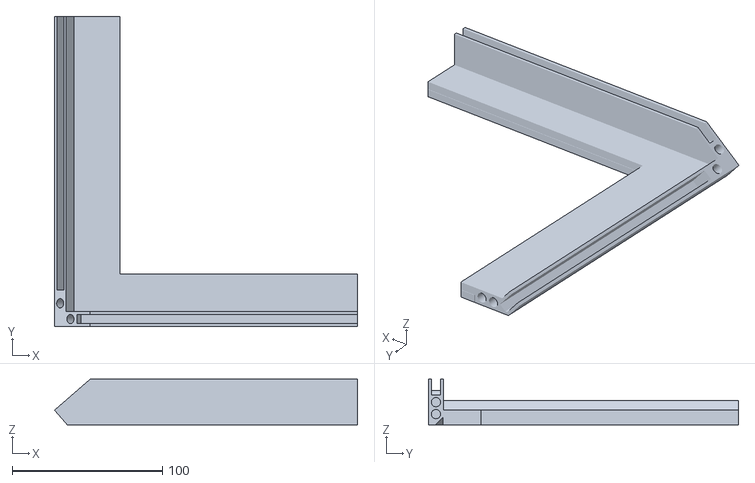
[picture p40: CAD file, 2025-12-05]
Huge slope 6mm plexiglass version/Face (Right Up).stl
201.7 x 206.5 x 30.5

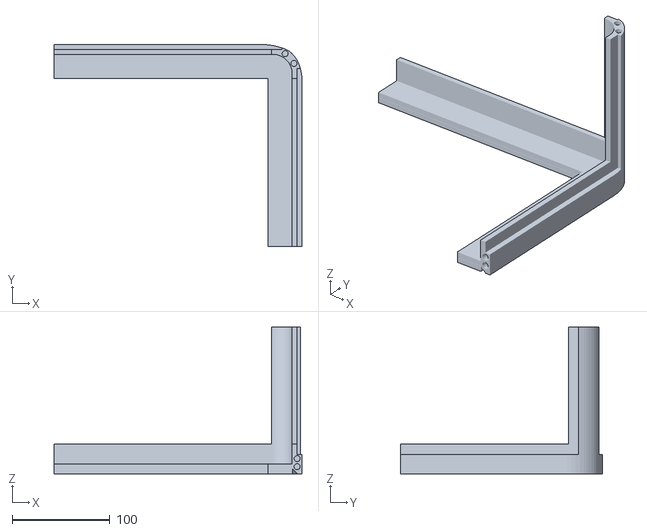
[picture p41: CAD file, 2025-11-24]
No slope version/Upper Front (Left).stl
253.5 x 206.5 x 150.0

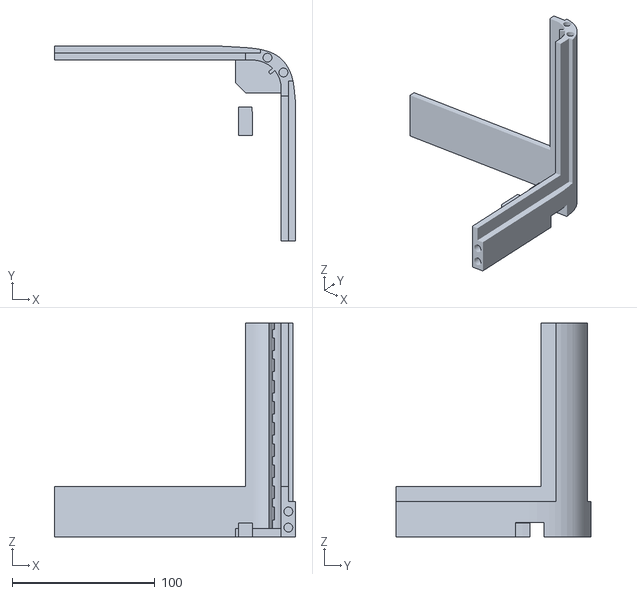
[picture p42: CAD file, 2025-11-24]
Smaller printer version/Bottom Back (Left).stl
169.0 x 137.1 x 150.0

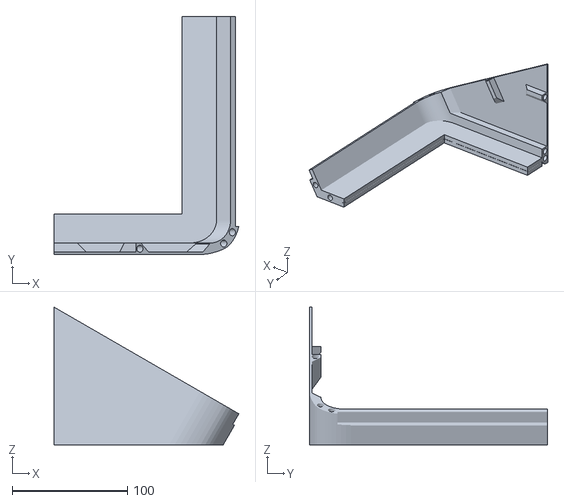
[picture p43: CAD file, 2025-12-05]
Front and slope plexiglass only version/Upper Face (Right Bottom).stl
160.3 x 206.5 x 119.5

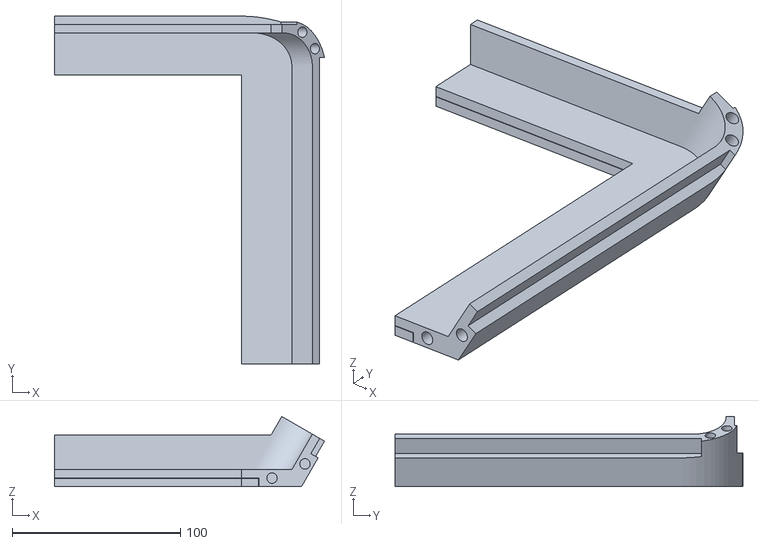
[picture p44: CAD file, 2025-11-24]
Original version/Upper Face (Left Bottom).stl
160.3 x 206.5 x 41.6

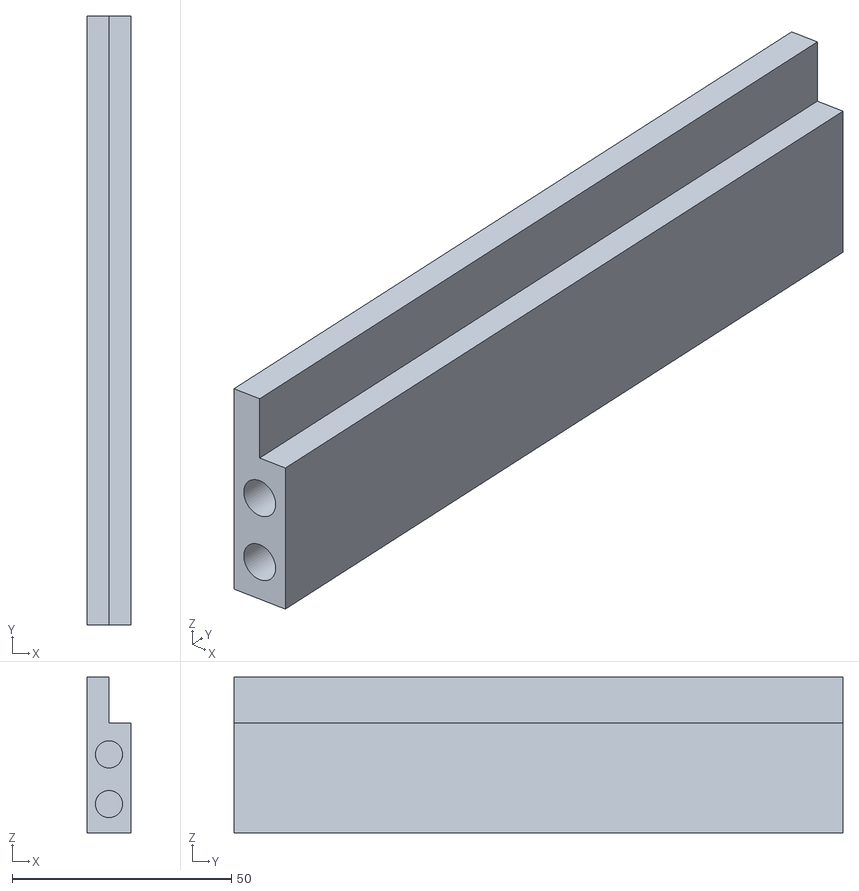
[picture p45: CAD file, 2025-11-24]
Smaller printer version/Bottom Back (Middle).stl
10.0 x 139.0 x 35.5

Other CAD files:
Front and slope plexiglass only version/Front Face (Left).stl
Original version/Upper Face (Right Up).stl
Huge slope 6mm plexiglass version/Top (Right).stl
No slope version/Upper Front (Right).stl
Front and slope plexiglass only version/Bottom Back (Left).stl
Front and slope plexiglass only version/Bottom Back (Right).stl
Front and slope plexiglass only version/Upper Face (Left Bottom).stl
Front and slope plexiglass only version/Upper Face (Left Up).stl
Front and slope plexiglass only version/Upper Face (Right Up).stl
Front and slope plexiglass only version/Upper Top (Left).stl
Front and slope plexiglass only version/Upper Top (Right).stl
Huge slope 6mm plexiglass version/Bottom Back (Left).stl
Huge slope 6mm plexiglass version/Bottom Back (Right).stl
Huge slope 6mm plexiglass version/Face (Left Bottom).stl
Huge slope 6mm plexiglass version/Face (Left Up).stl
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

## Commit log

2025-11-23 add one piece version
    [One piece version.stl]
2025-11-24 correct support
    [Upper Face (Left Bottom).stl, Upper Face (Left Up).stl, Upper Face (Right Bottom).stl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]
2025-11-24 add smaller printer version
    [Bottom Back (Left).stl, Bottom Back (Middle).stl, Bottom Back (Right).stl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]
2025-11-24 change folder name
    [Bottom Back (Left).stl, Bottom Back (Right).stl, Feet.stl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]
2025-11-28 Add huge slope version
    [Bottom Back (Left).stl, Bottom Back (Right).stl, Face (Left Bottom).stl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]
2025-12-05 modified readme.md and add new model
    [Bottom Back (Left).stl, Bottom Back (Right).stl, Calibrate.stl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]
2025-12-05 add huge slope one piece version
    [Feet.stl, Huge slope one piece version.stl]
2025-12-05 add huge slope 6mm plexiglass version
    [Bottom Back (Left).stl, Bottom Back (Right).stl, Face (Left Bottom).stl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]
